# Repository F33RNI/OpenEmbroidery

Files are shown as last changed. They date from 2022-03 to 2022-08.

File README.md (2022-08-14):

<h1 align="center">OpenEmbroidery</h1>

<div style="width:100%;text-align:center;">
    <p align="center">
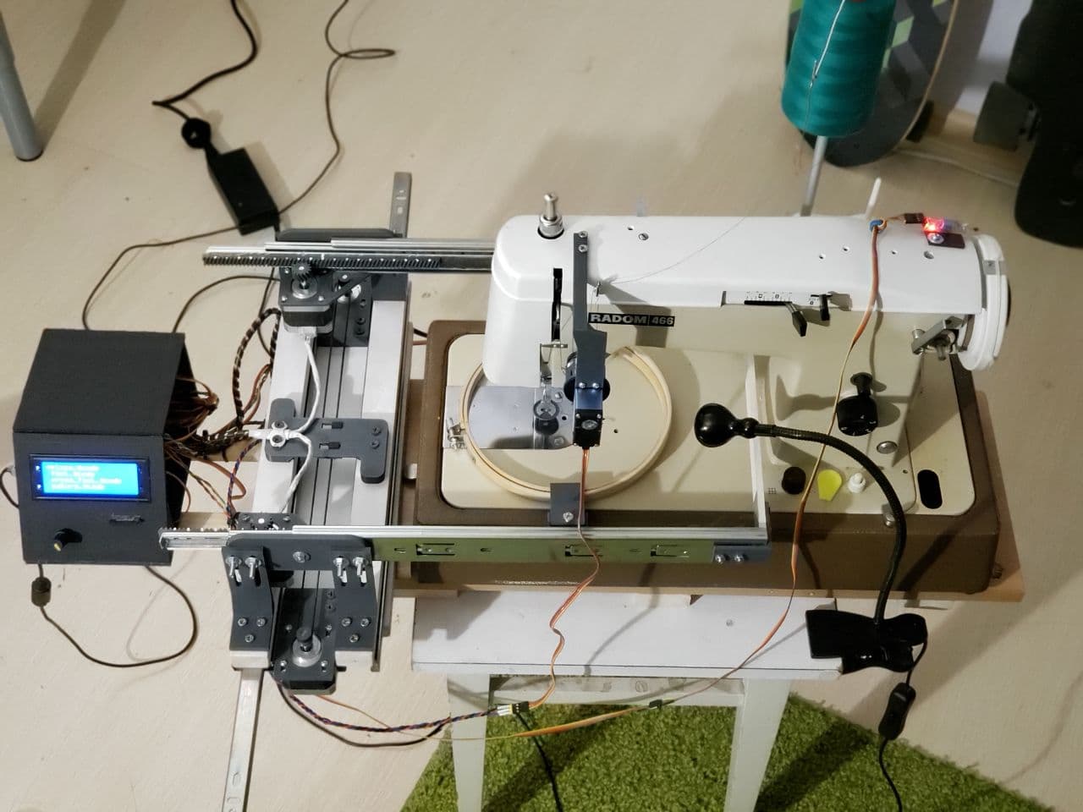
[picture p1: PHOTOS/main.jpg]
        
    </p>
</div>
<div style="width:100%;text-align:center;">
    <p align="center">
        
        
        
        
        
    </p>
</div>

----------

## What is it?

Open Embroidery is an open source project that allows you to turn an ordinary sewing machine into an embroidery machine

The fabric is fixed in the hoop, which moves with the help of stepper motors. For simplicity and versatility, embroidery patterns are pre-converted to G-Code using application written in Python.  
The whole process is controlled by Arduino Mega.  

----------

## Hardware

<div style="width:100%;text-align:center;">
    <p align="center">
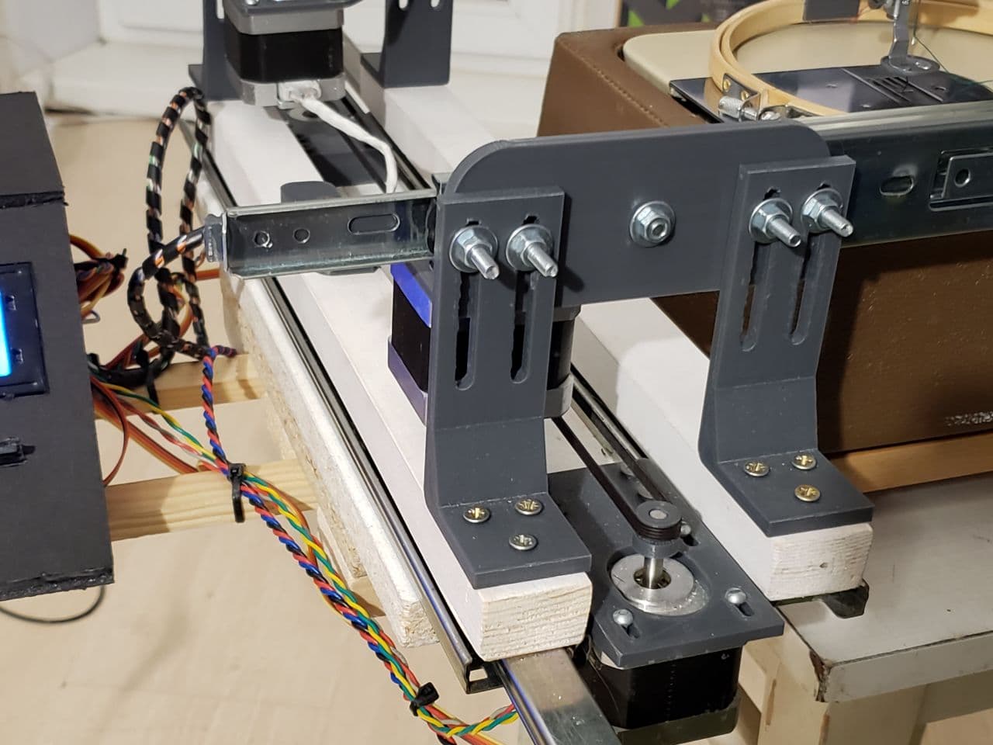
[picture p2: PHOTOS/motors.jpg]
        
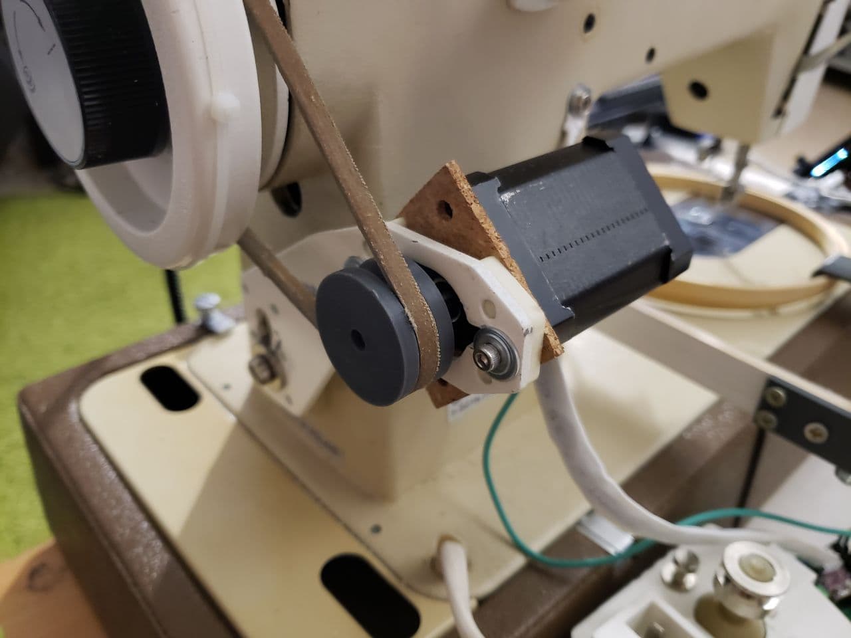
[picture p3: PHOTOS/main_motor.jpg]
        
    </p>
</div>

Hoop moves by standard NEMA 17 stepper motors (as in 3D printers). As drivers, you can use A4988 or DRV8825

<div style="width:100%;text-align:center;">
    <p align="center">
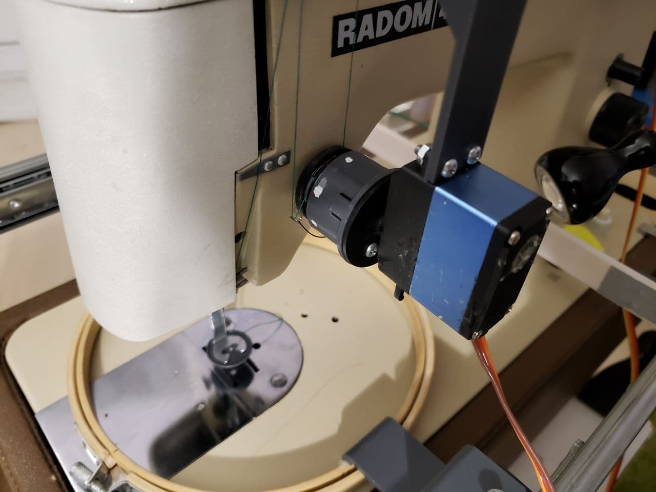
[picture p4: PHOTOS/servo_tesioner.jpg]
        
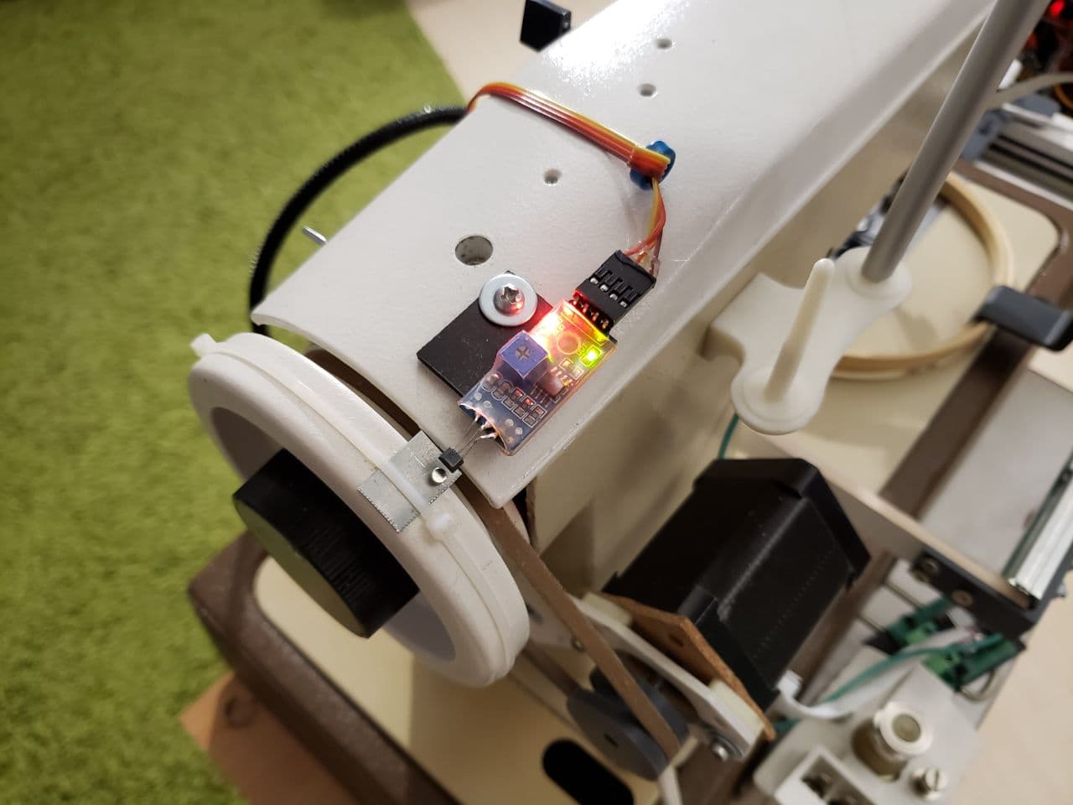
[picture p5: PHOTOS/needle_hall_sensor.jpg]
        
    </p>
</div>

In order to move the fabric (jump) - it is necessary to loosen the tension of the thread. This is done by a servo connected to the thread tensioner.

The fabric must be moved when the needle is in a certain position (same as in normal sewing). For synchronization, a hall sensor is used. When the magnet passes near the sensor, the main motor starts to decelerate and the tissue moves

<div style="width:100%;text-align:center;">
    <p align="center">
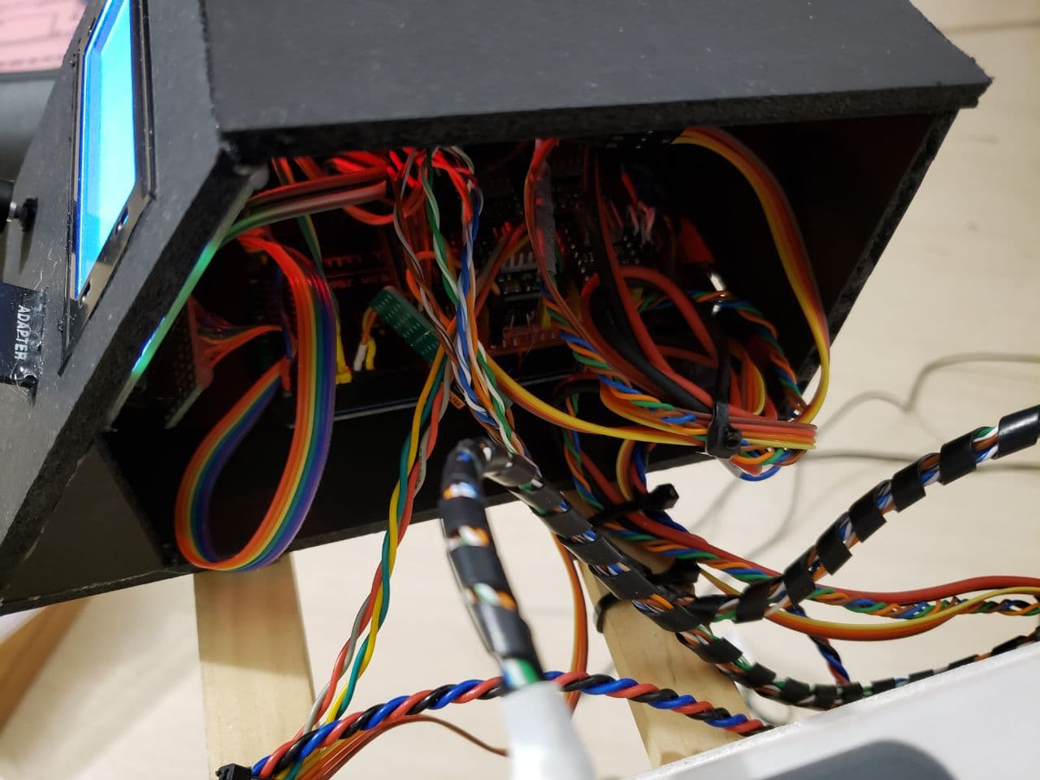
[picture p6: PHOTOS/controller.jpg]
        
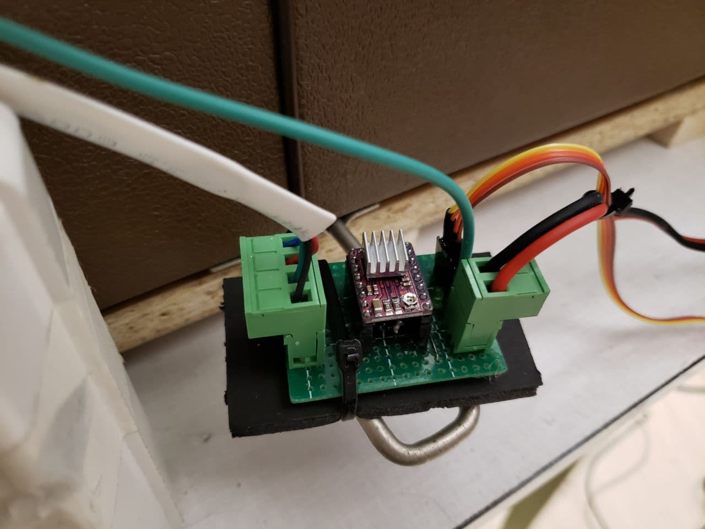
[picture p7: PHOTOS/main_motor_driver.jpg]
        
    </p>
</div>

G-Code files are read from the memory card. To control the entire system, one single rotary encoder with a button is used. To display information, a 20x4 display connected via the I2C bus is used.

----------

## Examples

<div style="width:100%;text-align:center;">
    <p align="center">
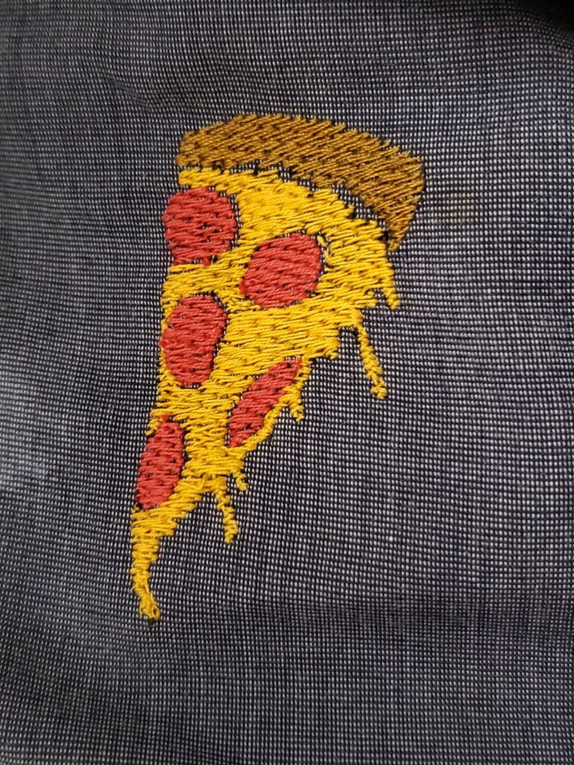
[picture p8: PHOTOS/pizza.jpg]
        
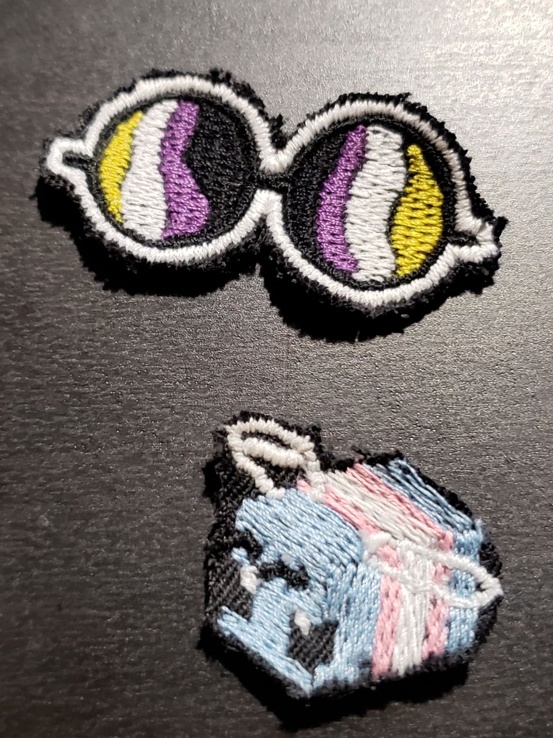
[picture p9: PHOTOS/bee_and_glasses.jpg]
        
    </p>
    <p align="center">
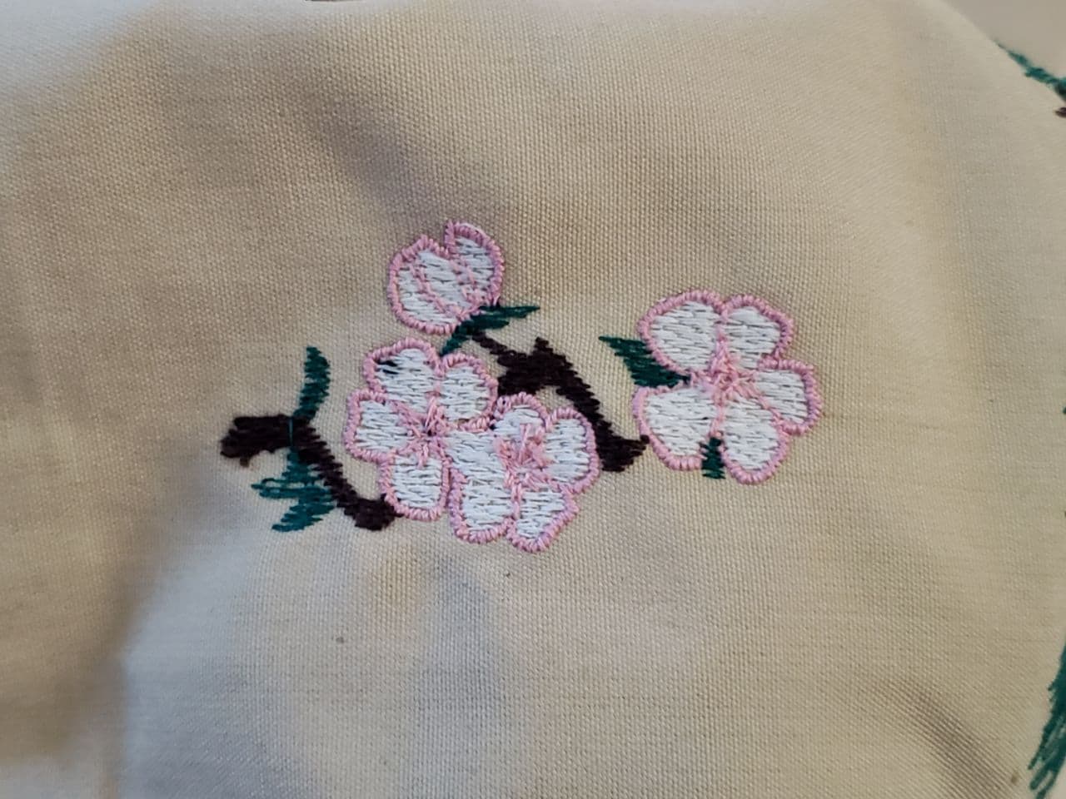
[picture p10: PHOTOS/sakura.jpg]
        
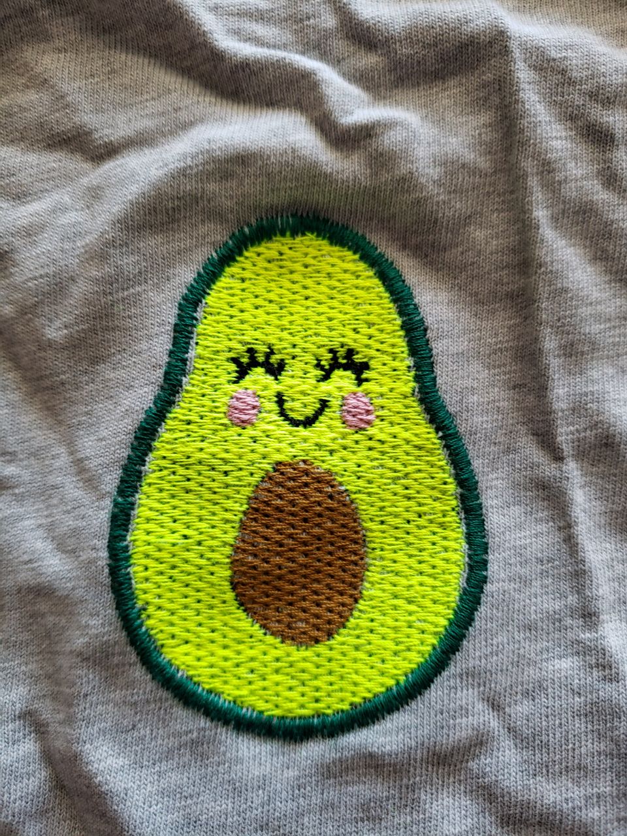
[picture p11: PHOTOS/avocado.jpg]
        
    </p>
</div>

This is just a small part of what this project can do...

.DST files can be found in `examples` folder

----------

## How to build this

Instruction is under development...

- At the start, you need to assemble a frame along which the hoop can move freely along two axes (as in the photos). In my case, drawer sliders were used. They are not very accurate, but their rigidity is usually sufficient.
- For movement, i used stepper motors with belts and racks. You need to move the hoop as quickly as possible, so it is recommended to use belts (used in 3d printers).
- To assemble the frame, you can find some parts in the 3D folder.
- Next, you need to assemble the electronics. I use 4 frame motor drivers (DRV8825 or A4988) and a DRV8825 driver at 40 volts to drive the sewing machine.
- For control panel, you need to connect an I2C display 20x4, a rotary encoder and a slot for a SD card (electronics schematic under development).
- For motors, set the current close to the maximum. (1.5-1.6A or 0.8V ref on driver for Nema17)
- After flashing the microcontroller, use OpenEmroidery.py to convert the embroidery template to a .gcode file, save it to a memory card and load it from the menu.

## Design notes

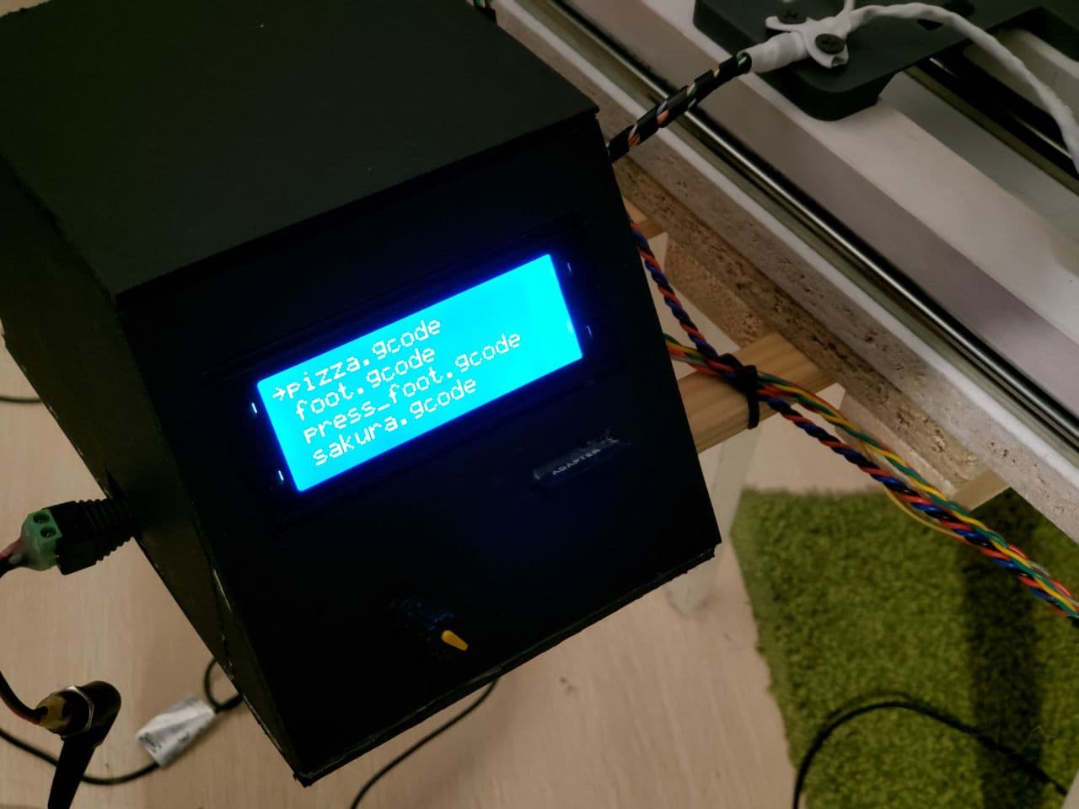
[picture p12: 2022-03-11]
PHOTOS/lcd.jpg

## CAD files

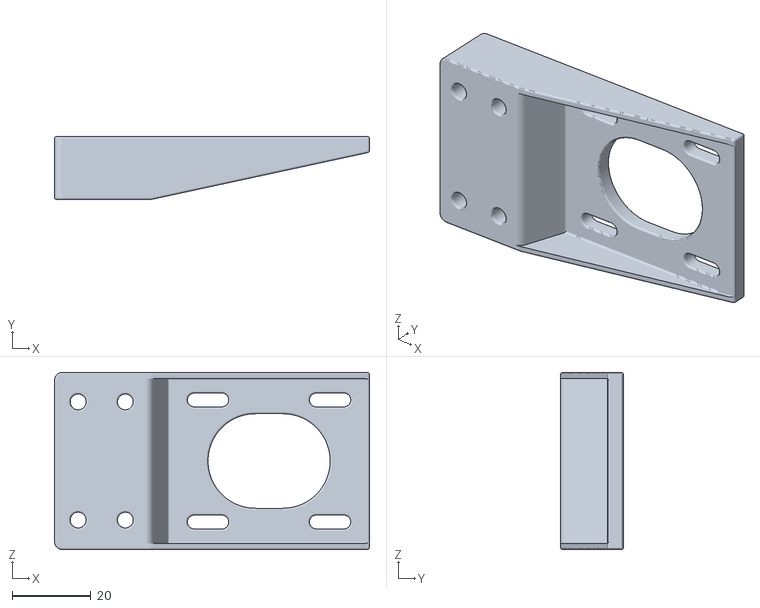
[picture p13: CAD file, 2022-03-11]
3D/main_motor_holder.stl
80.0 x 16.0 x 45.0

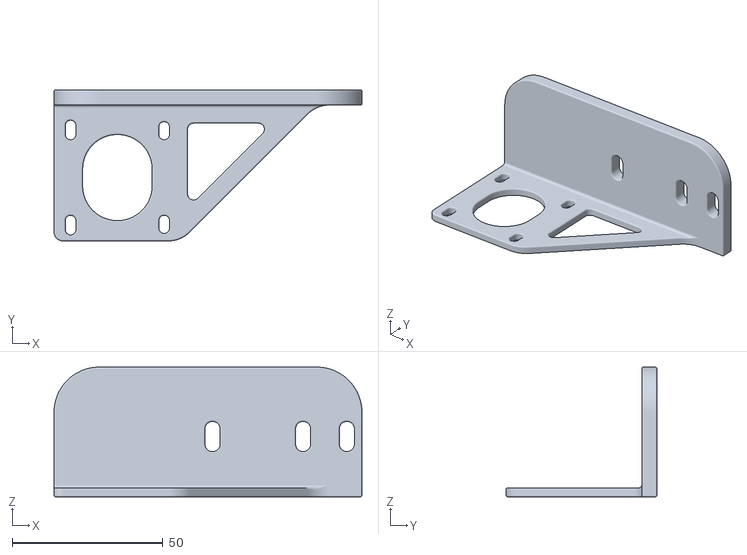
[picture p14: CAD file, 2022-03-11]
3D/side_motor_holder.stl
102.0 x 50.0 x 43.0

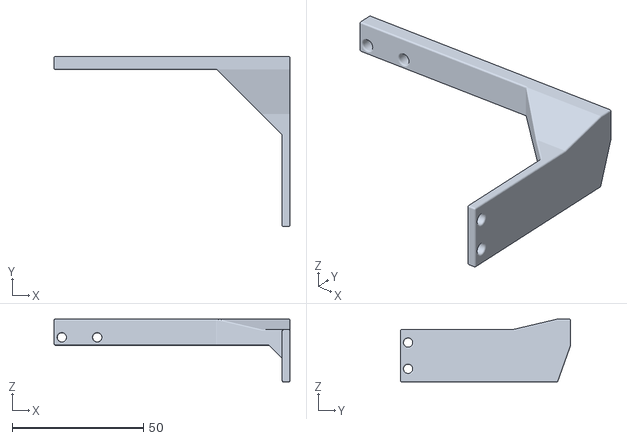
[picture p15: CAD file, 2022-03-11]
3D/servo_holder.stl
90.0 x 65.0 x 24.0

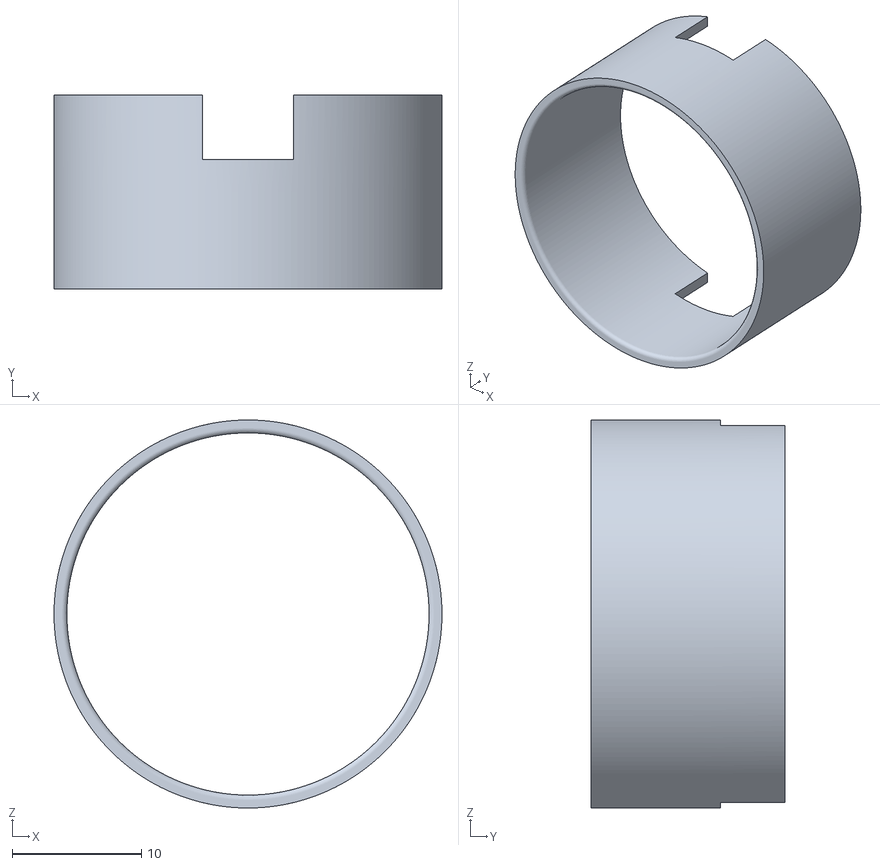
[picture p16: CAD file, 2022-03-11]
3D/tensioner_base.stl
30.0 x 15.0 x 30.0

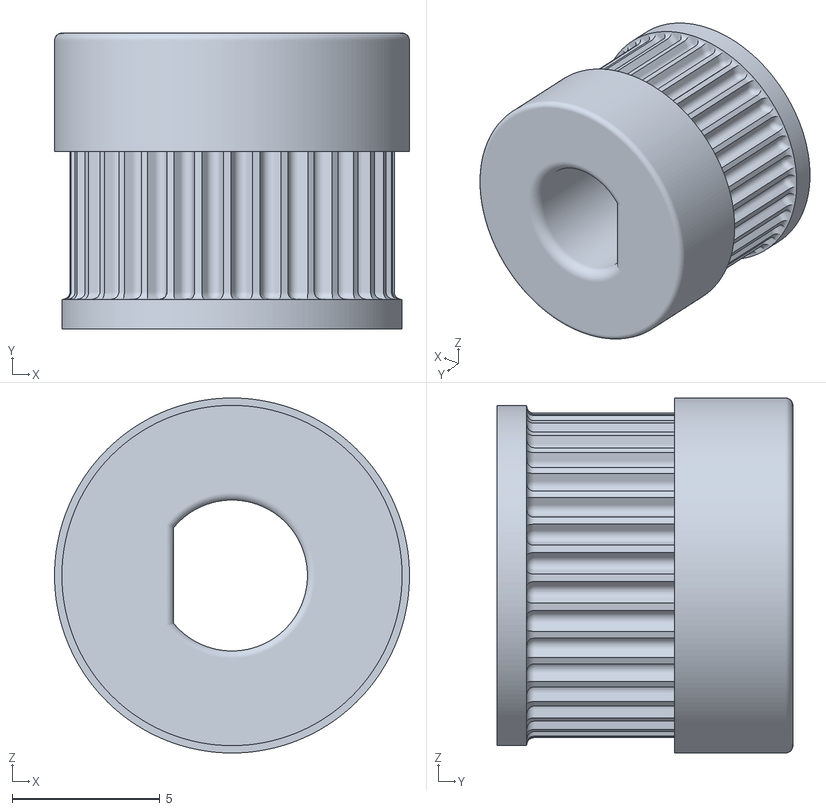
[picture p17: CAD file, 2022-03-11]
3D/belt_pulley.stl
12.0 x 10.0 x 12.0

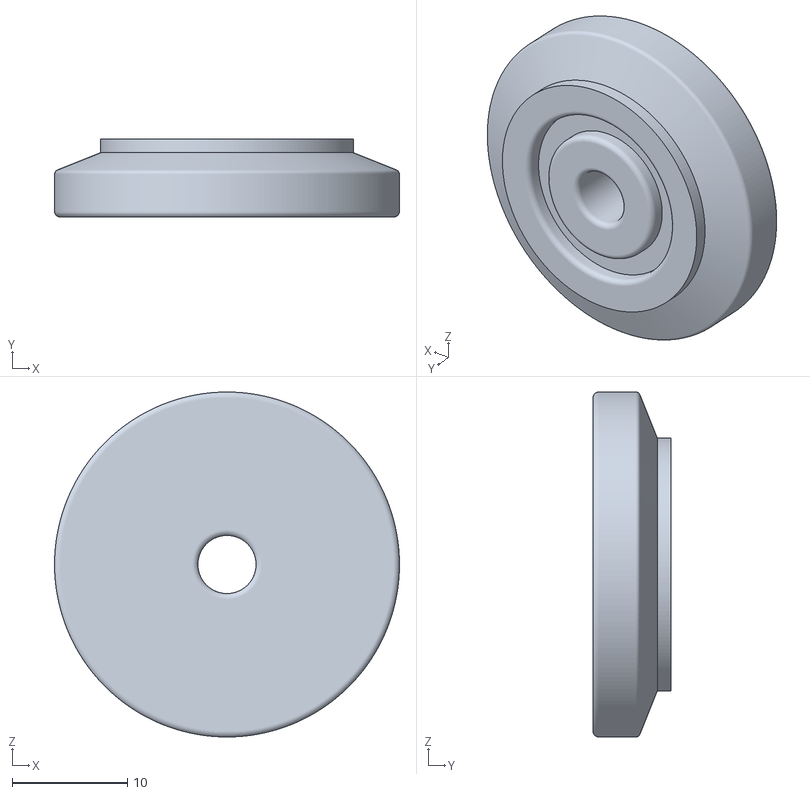
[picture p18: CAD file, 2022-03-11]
3D/pulley_part_2.stl
30.0 x 6.80 x 30.0

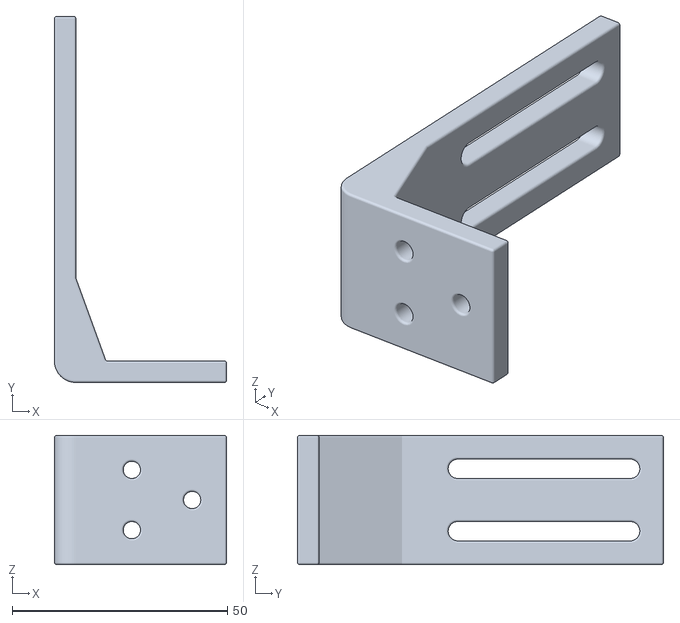
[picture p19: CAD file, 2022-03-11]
3D/angle.stl
40.0 x 85.0 x 30.0

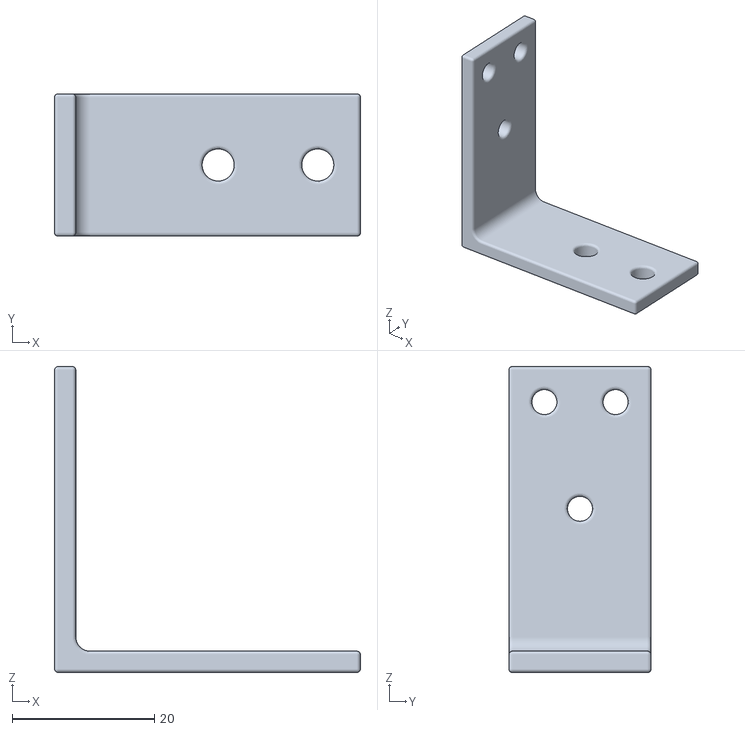
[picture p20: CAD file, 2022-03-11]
3D/angle_back.stl
43.0 x 20.0 x 43.0

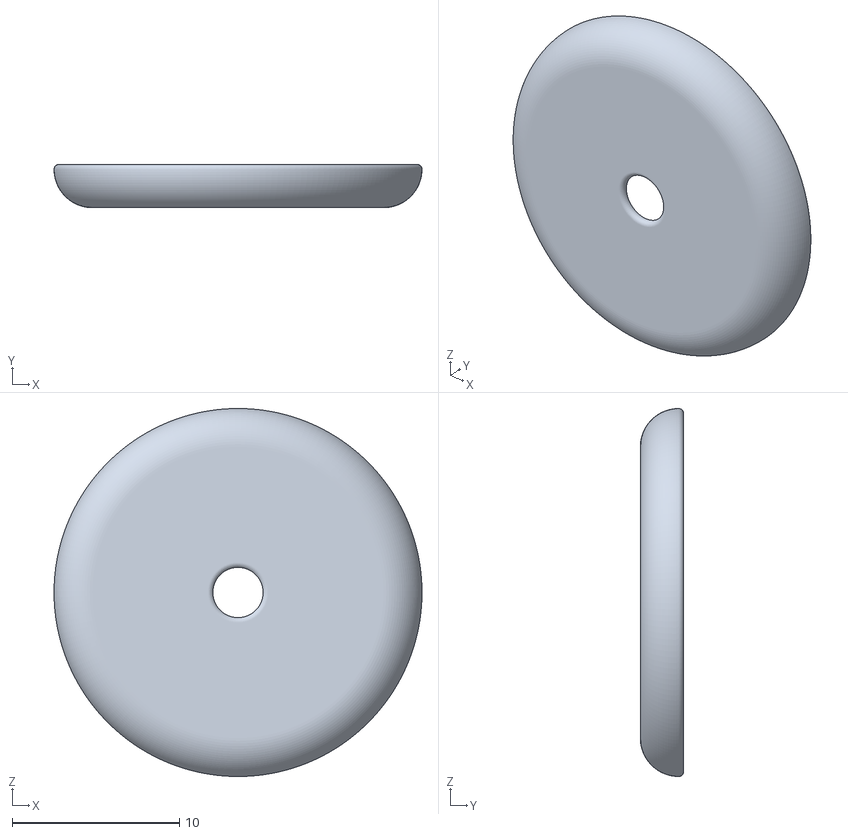
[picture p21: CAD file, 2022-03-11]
3D/foot.stl
22.0 x 2.60 x 22.0

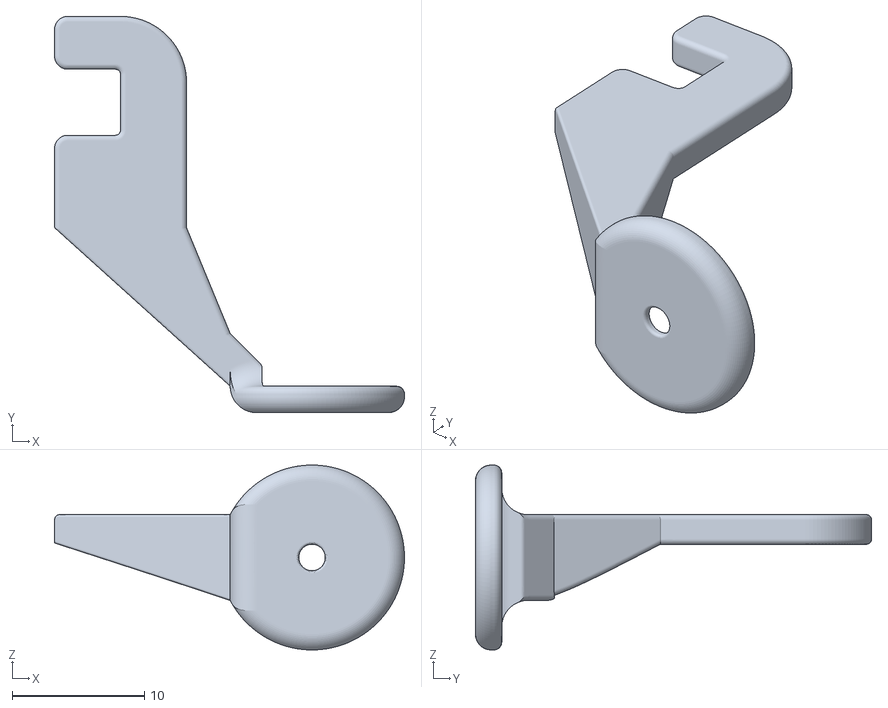
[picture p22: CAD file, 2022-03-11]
3D/press_foot.stl
26.5 x 30.0 x 14.0

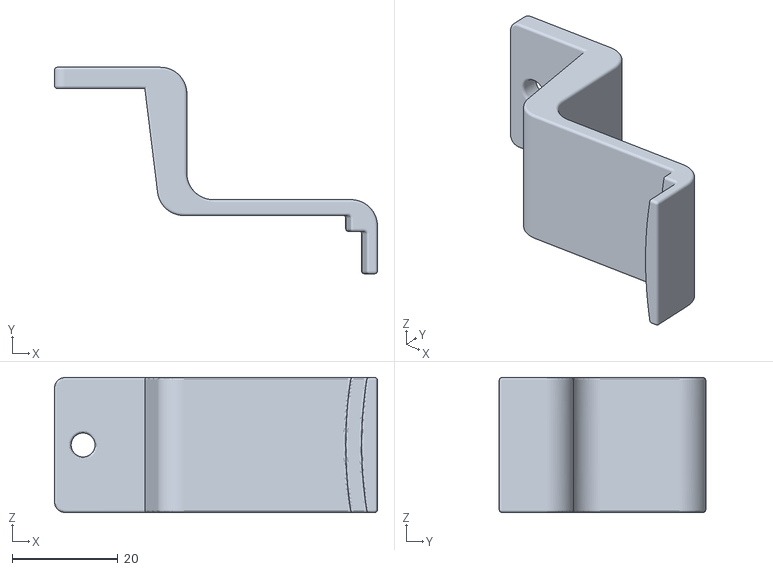
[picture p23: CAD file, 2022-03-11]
3D/hoop_adapter.stl
61.0 x 39.0 x 25.5

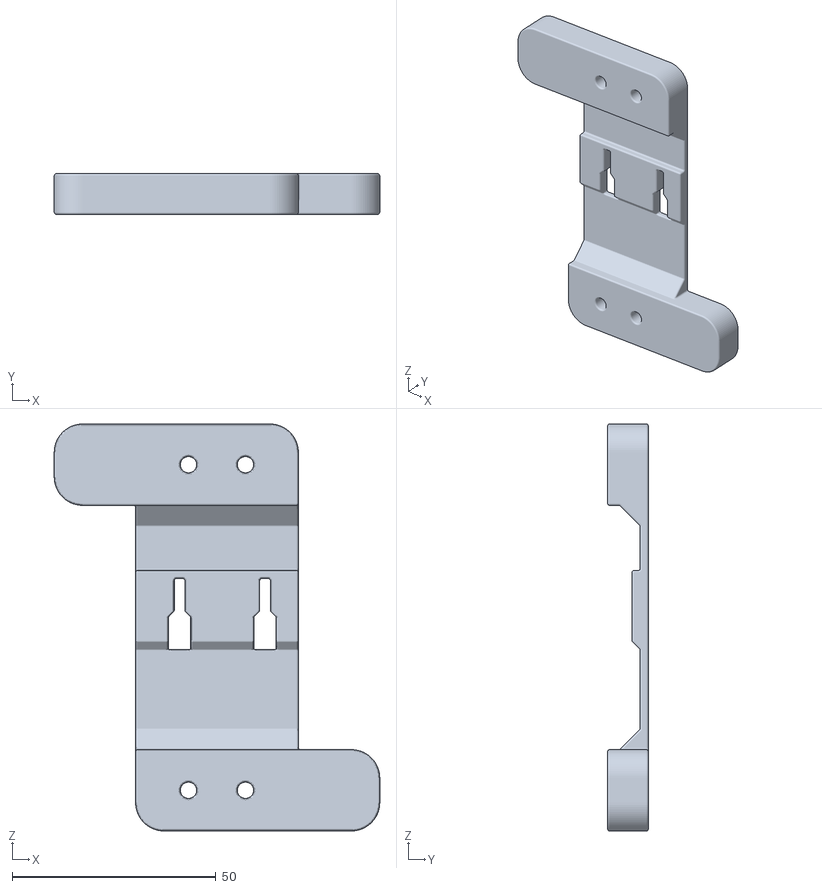
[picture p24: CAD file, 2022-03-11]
3D/belt_coupler.stl
80.0 x 10.0 x 100.0

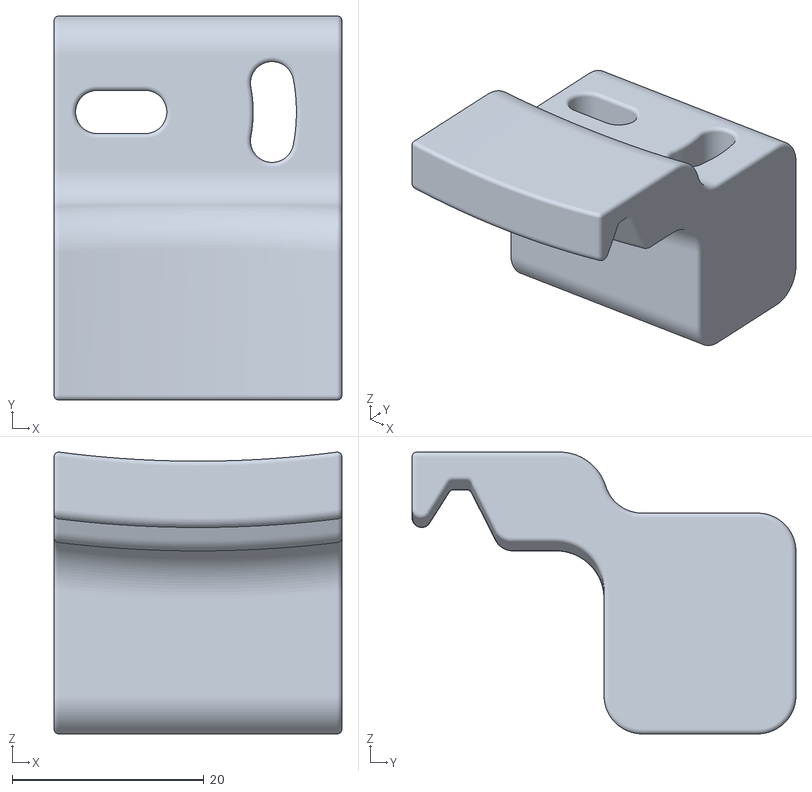
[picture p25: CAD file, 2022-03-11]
3D/hoop_holder.stl
30.0 x 40.0 x 29.4

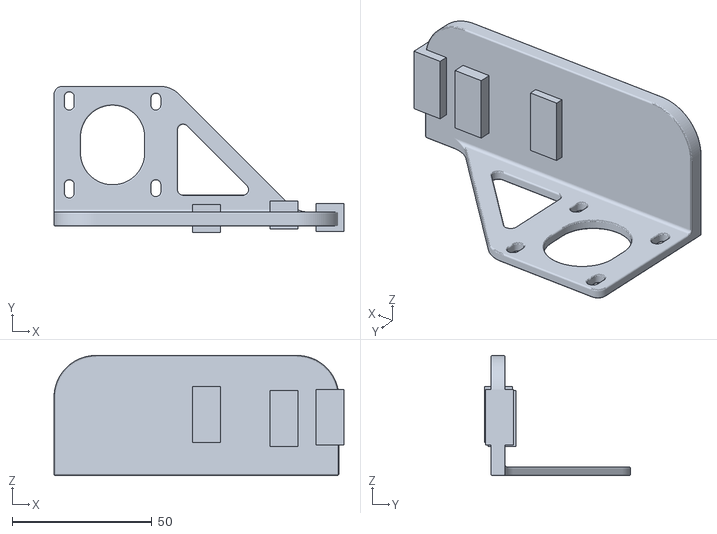
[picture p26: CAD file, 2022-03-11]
3D/side_motor_holder_mirrored.stl
103.9 x 52.4 x 43.0

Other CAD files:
3D/hoop_mount.stl
3D/pulley.stl
3D/pulley_part_1.stl
3D/tensioner_servo.stl
3D/angle.ipt
3D/angle_back.ipt
3D/belt_coupler.ipt
3D/belt_pulley.ipt
3D/foot.ipt
3D/hoop_adapter.ipt
3D/hoop_holder_158mm.ipt
3D/hoop_holder_9in.ipt
3D/hoop_mount.ipt
3D/main_motor_holder.ipt
3D/press_foot.ipt
3D/pulley.ipt
3D/pulley_part_1.ipt
3D/pulley_part_2.ipt
3D/servo_holder.ipt
3D/side_motor_holder.ipt
3D/tensioner_base.ipt
3D/tensioner_servo.ipt

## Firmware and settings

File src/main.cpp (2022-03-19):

/*
 * Copyright (C) 2022 Fern H., OpenEmbroidery project
 *
 * Licensed under the Apache License, Version 2.0 (the "License");
 * you may not use this file except in compliance with the License.
 * You may obtain a copy of the License at
 *
 *      http://www.apache.org/licenses/LICENSE-2.0
 *
 * Unless required by applicable law or agreed to in writing, software
 * distributed under the License is distributed on an "AS IS" BASIS,
 * See the License for the specific language governing permissions and
 * limitations under the License.
 *
 * IN NO EVENT SHALL THE AUTHOR BE LIABLE FOR ANY CLAIM, DAMAGES OR
 * OTHER LIABILITY, WHETHER IN AN ACTION OF CONTRACT, TORT OR OTHERWISE,
 * ARISING FROM, OUT OF OR IN CONNECTION WITH THE SOFTWARE OR THE USE OR
 * OTHER DEALINGS IN THE SOFTWARE.
 *
 */

#include "config.hpp"
#include "datatypes.hpp"

volatile uint8_t system_state;

#ifdef DEBUG
HardwareSerial* serial;
#endif

void setup() {
  // Initialize debug serial port
#ifdef DEBUG
  Serial.begin(DEBUG_SERIAL_SPEED);
  serial = &DEBUG_SERIAL;
#endif

  // Initialize LCD and print startup message
  lcd_setup();

  // Initialize rotary encoder
  encoder_setup();

  // Initialize stepper motors
  if (!motors_setup()) {
    // Print error if motors setup error
    lcd_print_error(F("Motors init. failed"));

    // Enter infinite loop
    while (1);
  }

  // Initialize needle sensor
  needle_sensor_setup();

  // Initialize servo
  servo_setup();

  // Initialize speed controller
  //speed_controller_setup();

  // Initialize gcode handler
  gcode_clear();

  // Initialize SD card
  if (!sd_card_setup()) {
    // Print error if SD card is not detected or the card cannot be opened
    lcd_print_error(F("SD card init. failed"));

    // Enter infinite loop
    while (1);
  }

  // Count number of files on SD card
  sd_card_count_files();

  // Wait some time to finish initialization (also, delay for startup message)
  delay(500);

  // Reset encoder
  encoder_reset_counter();
  encoder_clear_button_flag();

  // Show SD-card menu
  menu_sd_card_init();
}

void loop() {
  switch (system_state)
  {
  case STATE_PRE_START:
    // Pre-start menu
    menu_pre_start();
    break;

  case STATE_WORK:
  case STATE_TENSION_SETUP:
    // Working
    gcode_cycle();
    if (system_state == STATE_TENSION_SETUP)
      menu_tension();
    else
      menu_work();
    break;

  case STATE_PAUSE:
    // Pause
    menu_pause();
    break;

  case STATE_STOP_CONFIRMATION:
    // Stop confirmation
    menu_stop_confirmation();
    break;
  
  default:
    // SD-card menu
    menu_sd_card();
    break;
  }
}

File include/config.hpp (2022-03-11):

/*
 * Copyright (C) 2022 Fern H., OpenEmbroidery project
 *
 * Licensed under the Apache License, Version 2.0 (the "License");
 * you may not use this file except in compliance with the License.
 * You may obtain a copy of the License at
 *
 *      http://www.apache.org/licenses/LICENSE-2.0
 *
 * Unless required by applicable law or agreed to in writing, software
 * distributed under the License is distributed on an "AS IS" BASIS,
 * See the License for the specific language governing permissions and
 * limitations under the License.
 *
 * IN NO EVENT SHALL THE AUTHOR BE LIABLE FOR ANY CLAIM, DAMAGES OR
 * OTHER LIABILITY, WHETHER IN AN ACTION OF CONTRACT, TORT OR OTHERWISE,
 * ARISING FROM, OUT OF OR IN CONNECTION WITH THE SOFTWARE OR THE USE OR
 * OTHER DEALINGS IN THE SOFTWARE.
 *
 */

#ifndef CONFIG_H
#define CONFIG_H

#include <Arduino.h>


/*******************************/
/*            DEBUG            */
/*******************************/
//#define DEBUG

#ifdef DEBUG
#define DEBUG_SERIAL Serial
#define DEBUG_SERIAL_SPEED 115200
#endif


/**********************************************/
/*            CNC Shield v1.0 pins            */
/**********************************************/
// Step pins
const uint8_t PIN_X_STP PROGMEM = 2;
const uint8_t PIN_Y_STP PROGMEM = 3;
const uint8_t PIN_Z_STP PROGMEM = 5;

// Dir pins
const uint8_t PIN_X_DIR PROGMEM = 7;
const uint8_t PIN_Y_DIR PROGMEM = 6;

// Enable pin
const uint8_t PIN_ENABLE PROGMEM = 8;
const uint8_t PIN_ENABLE_Z PROGMEM = 9;


/*********************************/
/*            Encoder            */
/*********************************/
const uint8_t PIN_ENC_A PROGMEM = A8;
const uint8_t PIN_ENC_B PROGMEM = A10;
const uint8_t PIN_ENC_BTN PROGMEM = A11;
const uint8_t PIN_ENC_GND PROGMEM = A9;
#define ENCODER_PCINT_VECT PCINT2_vect
// 0 or 1
#define ENC_TYPE 0
#define MIN_BTN_PRESSED_TIME 100


/********************************************/
/*            Needle sensor pins            */
/********************************************/
const uint8_t PIN_NEEDLE_SENSOR PROGMEM = 19;


/***************************************/
/*            Tension servo            */
/***************************************/
const uint8_t PIN_SERVO PROGMEM = 11;
# define SERVO_LOW_TENSION_US 800
# define SERVO_HIGH_TENSION_US 2200


/******************************************/
/*            Speed controller            */
/******************************************/
const uint8_t SPEED_CONTROLLER_PIN PROGMEM = 46;


/*********************************/
/*            SD Card            */
/*********************************/
const uint8_t PIN_SD_CARD_CS = 53;
// SD_FAT_TYPE = 0 for SdFat/File as defined in SdFatConfig.h,
// 1 for FAT16/FAT32, 2 for exFAT, 3 for FAT16/FAT32 and exFAT.
#define SD_FAT_TYPE 0
#define FILE_EXT_UPPER ".GCODE"
#define FILE_EXT_LOWER ".gcode"
#define MAX_FILE_NAME_LENGTH 50
#define MAX_GCODE_LINE_LENGTH 50


/****************************************/
/*            Stepper motors            */
/****************************************/
#define FAS_TIMER_MODULE 3
const int32_t STEPS_PER_MM_X PROGMEM = 90;
const int32_t STEPS_PER_MM_Y PROGMEM = 65;
#define SPEED_INITIAL_XY_MM_S 10
#define SPEED_INITIAL_Z_HZ 200
#define ACCELERATION_INITIAL_X_MM_S 300
#define ACCELERATION_INITIAL_Y_MM_S 500
#define ACCELERATION_INITIAL_Z_HZ 10000

// 15000 1200

#endif

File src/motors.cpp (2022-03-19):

/*
 * Copyright (C) 2022 Fern H., OpenEmbroidery project
 *
 * Licensed under the Apache License, Version 2.0 (the "License");
 * you may not use this file except in compliance with the License.
 * You may obtain a copy of the License at
 *
 *      http://www.apache.org/licenses/LICENSE-2.0
 *
 * Unless required by applicable law or agreed to in writing, software
 * distributed under the License is distributed on an "AS IS" BASIS,
 * See the License for the specific language governing permissions and
 * limitations under the License.
 *
 * IN NO EVENT SHALL THE AUTHOR BE LIABLE FOR ANY CLAIM, DAMAGES OR
 * OTHER LIABILITY, WHETHER IN AN ACTION OF CONTRACT, TORT OR OTHERWISE,
 * ARISING FROM, OUT OF OR IN CONNECTION WITH THE SOFTWARE OR THE USE OR
 * OTHER DEALINGS IN THE SOFTWARE.
 *
 */

#include "config.hpp"
#include "datatypes.hpp"
#include "motors.hpp"

/**
 * @brief Initializes stepper motors with FastAccelStepper library
 * 
 * @return boolean - true is successful
 */
boolean motors_setup() {
    // Add motors to the FastAccelStepper
    engine.init();
    stepper_x = engine.stepperConnectToPin(PIN_X_STP);
    stepper_y = engine.stepperConnectToPin(PIN_Y_STP);
    stepper_z = engine.stepperConnectToPin(PIN_Z_STP);

    // Return false if initialization fails
    if (!stepper_x || !stepper_y || !stepper_z)
        return false;

    // Set enable and direction pins
    stepper_x->setDirectionPin(PIN_X_DIR);
    stepper_x->setEnablePin(PIN_ENABLE);
    stepper_y->setDirectionPin(PIN_Y_DIR);
    stepper_y->setEnablePin(PIN_ENABLE);
    stepper_z->setEnablePin(PIN_ENABLE_Z);

    // Disable motors
    motors_disable();
    stepper_z->disableOutputs();

    // Set default speed and acceleration
    stepper_x->setSpeedInHz(SPEED_INITIAL_XY_MM_S * STEPS_PER_MM_X);
    stepper_y->setSpeedInHz(SPEED_INITIAL_XY_MM_S * STEPS_PER_MM_Y);
    stepper_z->setSpeedInHz(SPEED_INITIAL_Z_HZ);
    stepper_x->setAcceleration(ACCELERATION_INITIAL_X_MM_S * STEPS_PER_MM_X);
    stepper_y->setAcceleration(ACCELERATION_INITIAL_Y_MM_S * STEPS_PER_MM_Y);
    stepper_z->setAcceleration(ACCELERATION_INITIAL_Z_HZ);
    
    // Return successful value
    return true;
}

/**
 * @brief Gets current x motor position
 * 
 * @return float - motor position in mm
 */
float motors_get_x() {
    return (float)stepper_x->getCurrentPosition() / (float)STEPS_PER_MM_X;
}

/**
 * @brief Gets current y motor position
 * 
 * @return float - motor position in mm
 */
float motors_get_y() {
    return (float)stepper_y->getCurrentPosition() / (float)STEPS_PER_MM_Y;
}

/**
 * @brief Sets X motor speed
 * 
 * @param speed_mm_s - speed in mm/s
 */
void motors_set_speed_x(float speed_mm_s) {
    stepper_x->setSpeedInHz(speed_mm_s * STEPS_PER_MM_X);
}

/**
 * @brief Sets Y motor speed
 * 
 * @param speed_mm_s - speed in mm/s
 */
void motors_set_speed_y(float speed_mm_s) {
    stepper_y->setSpeedInHz(speed_mm_s * STEPS_PER_MM_Y);
}

/**
 * @brief Sets Z motor speed
 * 
 * @param speed_hz - speed in steps/s
 */
void motors_set_speed_z(uint32_t speed_hz) {
    stepper_z->setSpeedInHz(speed_hz);
}

/**
 * @brief Sets X motor acceleration
 * 
 * @param acceleration_mm_s - acceleration in mm/s^2
 */
void motors_set_acceleration_x(float acceleration_mm_s) {
    stepper_x->setAcceleration(acceleration_mm_s * STEPS_PER_MM_X);
}

/**
 * @brief Sets Y motor acceleration
 * 
 * @param acceleration_mm_s - acceleration in mm/s^2
 */
void motors_set_acceleration_y(float acceleration_mm_s) {
    stepper_y->setAcceleration(acceleration_mm_s * STEPS_PER_MM_Y);
}

/**
 * @brief Sets Z motor acceleration
 * 
 * @param acceleration_steps_s - acceleration in steps/s^2
 */
void motors_set_acceleration_z(int32_t acceleration_steps_s) {
    stepper_z->setAcceleration(acceleration_steps_s);
}

/**
 * @brief Starts moving to absolute position
 * Attention! Blocks the thread until the steppers start moving
 * 
 * @param x - new absolute X position in mm
 * @param y - new absolute Y position in mm
 */
void motors_move_to_position(float *x, float *y) {
    // Calculate new position in steps
    new_position_x_steps = *x * (float)STEPS_PER_MM_X;
    new_position_y_steps = *y * (float)STEPS_PER_MM_Y;

    // Check if it is a new position
    if (new_position_x_steps != stepper_x->getCurrentPosition()
        || new_position_y_steps != stepper_y->getCurrentPosition()) {
            // Move to new position
            stepper_x->moveTo(new_position_x_steps);
            stepper_y->moveTo(new_position_y_steps);

            // Wait for stepper to start moving
            while (!stepper_x->isRunning() && !stepper_y->isRunning());
        }
}

/**
 * @brief Enables motor drivers
 * 
 */
void motors_enable(void) {
    // Enable motor drivers
    stepper_x->enableOutputs();
    stepper_y->enableOutputs();
}

/**
 * @brief Disables motor drivers
 * 
 */
void motors_disable(void) {
    // Disable motor drivers
    stepper_x->disableOutputs();
    stepper_y->disableOutputs();
}

/**
 * @brief Checks if motors are stopped
 * 
 * @return boolean - true if motors are stopped
 */
boolean is_motors_stopped() {
    /*boolean stepper_x_decelerating_or_stopped = !stepper_x->isRunning()
        || stepper_x->rampState() == RAMP_STATE_DECELERATE
        || stepper_x->rampState() == RAMP_STATE_DECELERATE_TO_STOP
        || stepper_x->rampState() == RAMP_STATE_DECELERATING_FLAG;

    boolean stepper_y_decelerating_or_stopped = !stepper_y->isRunning()
        || stepper_y->rampState() == RAMP_STATE_DECELERATE
        || stepper_y->rampState() == RAMP_STATE_DECELERATE_TO_STOP
        || stepper_y->rampState() == RAMP_STATE_DECELERATING_FLAG;

    return stepper_x_decelerating_or_stopped && stepper_y_decelerating_or_stopped;*/

    return !stepper_x->isRunning() && !stepper_y->isRunning();
}

/**
 * @brief Stops motors with deceleration
 * 
 */
void motors_stop(void) {
    stepper_x->stopMove();
    stepper_y->stopMove();
}

/**
 * @brief Force stops and disables motors
 * 
 */
void motors_abort_and_reset(void) {
    // Stop motors without deceleration
    stepper_x->forceStop();
    stepper_y->forceStop();

    // Disable motor drivers
    motors_disable();

    // Reset absolute position
    stepper_x->setCurrentPosition(0);
    stepper_y->setCurrentPosition(0);
}

/**
 * @brief Enable output of Z motor
 * 
 */
void motors_enable_z(void) {
    stepper_z->enableOutputs();
}

/**
 * @brief Disables output of Z motor
 * 
 */
void motors_disable_z(void) {
    stepper_z->disableOutputs();
}

/**
 * @brief Start spinning z motor
 * 
 */
void motors_start_z(void) {
    stepper_z->moveByAcceleration(stepper_z->getAcceleration());
}

/**
 * @brief Stops spinning z motor
 * 
 */
void motors_stop_z(void) {
    stepper_z->stopMove();
}

/**
 * @brief Checks if Z motor is stopped
 * 
 * @return boolean - true if motor is stopped
 */
boolean is_motor_z_stopped() {
    return !stepper_z->isRunning();
}

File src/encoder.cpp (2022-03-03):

/*
 * Copyright (C) 2022 Fern H., OpenEmbroidery project
 *
 * Licensed under the Apache License, Version 2.0 (the "License");
 * you may not use this file except in compliance with the License.
 * You may obtain a copy of the License at
 *
 *      http://www.apache.org/licenses/LICENSE-2.0
 *
 * Unless required by applicable law or agreed to in writing, software
 * distributed under the License is distributed on an "AS IS" BASIS,
 * See the License for the specific language governing permissions and
 * limitations under the License.
 *
 * IN NO EVENT SHALL THE AUTHOR BE LIABLE FOR ANY CLAIM, DAMAGES OR
 * OTHER LIABILITY, WHETHER IN AN ACTION OF CONTRACT, TORT OR OTHERWISE,
 * ARISING FROM, OUT OF OR IN CONNECTION WITH THE SOFTWARE OR THE USE OR
 * OTHER DEALINGS IN THE SOFTWARE.
 *
 */

#include "config.hpp"
#include "datatypes.hpp"
#include "encoder.hpp"

/**
 * @brief Initializes encoder pins and interrupts
 */
void encoder_setup(void) {
#ifdef DEBUG
    serial->println("Initializing encoder");
#endif
    // Initialize encoder pins as pull up inputs
    pinMode(PIN_ENC_A, INPUT_PULLUP);
    pinMode(PIN_ENC_B, INPUT_PULLUP);
    pinMode(PIN_ENC_BTN, INPUT_PULLUP);

    // Initialize encoder ground
    pinMode(PIN_ENC_GND, OUTPUT);
    digitalWrite(PIN_ENC_GND, 0);

    // Convert arduino pins to input register
    enc_a_in_reg = portInputRegister(digitalPinToPort(PIN_ENC_A));
    enc_b_in_reg = portInputRegister(digitalPinToPort(PIN_ENC_B));
    enc_btn_in_reg = portInputRegister(digitalPinToPort(PIN_ENC_BTN));

    // Convert arduino pins to masks
    enc_a_mask = digitalPinToBitMask(PIN_ENC_A);
    enc_b_mask = digitalPinToBitMask(PIN_ENC_B);
    enc_btn_mask = digitalPinToBitMask(PIN_ENC_BTN);

    // Enable PCINT
    *digitalPinToPCMSK(PIN_ENC_A) |= bit (digitalPinToPCMSKbit(PIN_ENC_A));
    *digitalPinToPCMSK(PIN_ENC_B) |= bit (digitalPinToPCMSKbit(PIN_ENC_B));
    *digitalPinToPCMSK(PIN_ENC_BTN) |= bit (digitalPinToPCMSKbit(PIN_ENC_BTN));

    // Clear any outstanding interrupt and enable interrupt for the groups
    PCIFR  |= bit (digitalPinToPCICRbit(PIN_ENC_A));
    PCICR  |= bit (digitalPinToPCICRbit(PIN_ENC_A));
    PCIFR  |= bit (digitalPinToPCICRbit(PIN_ENC_B));
    PCICR  |= bit (digitalPinToPCICRbit(PIN_ENC_B));
    PCIFR  |= bit (digitalPinToPCICRbit(PIN_ENC_BTN));
    PCICR  |= bit (digitalPinToPCICRbit(PIN_ENC_BTN));
}

/**
 * @brief Construct a new ISR object
 * 
 */
ISR(ENCODER_PCINT_VECT) {
    // Read current states
    enc_a_state = !(*enc_a_in_reg & enc_a_mask);
    enc_b_state = !(*enc_b_in_reg & enc_b_mask);
    enc_btn_state = !(*enc_btn_in_reg & enc_btn_mask);

    // If encoder state changed
    if (enc_a_state != enc_a_state_last) {
        enc_turn_flag = !enc_turn_flag;

        // Increment or decrement encoder_counter
#if (ENC_TYPE == 1)
        if (enc_turn_flag)
            encoder_counter += (enc_b_state != enc_a_state_last) ? -1 : 1;
#else
        encoder_counter += (enc_b_state != enc_a_state_last) ? -1 : 1;
#endif

        // Store A pin state for next cycle
        enc_a_state_last = enc_a_state;

    }

    // Button pressed
    if (enc_btn_state && !enc_btn_state_last) {
        // Start timer
        button_timer = millis();

        // Store button state for next cycle
        enc_btn_state_last = enc_btn_state;
    }

    // Button released
    else if (!enc_btn_state && enc_btn_state_last) {
        // Set button flag
        if (millis() - button_timer >= MIN_BTN_PRESSED_TIME)
            button_pressed_flag = true;

        // Store button state for next cycle
        enc_btn_state_last = enc_btn_state;
    }
}

/**
 * @brief Returns encoder counter
 * 
 * @return int32_t - encoder counter
 */
int32_t encoder_get_counter() {
    return encoder_counter;
}

/**
 * @brief Returns button_pressed_flag
 * 
 * @return boolean - true if button was pressed
 */
boolean encoder_get_button_flag() {
    return button_pressed_flag;
}

/**
 * @brief Clears encoder_counter
 * 
 */
void encoder_reset_counter(void) {
    encoder_counter = 0;
}

/**
 * @brief Clears button_pressed_flag
 * 
 */
void encoder_clear_button_flag(void) {
    button_pressed_flag = false;
}
